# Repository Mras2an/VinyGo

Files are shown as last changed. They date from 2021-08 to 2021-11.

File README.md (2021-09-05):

# VinyGo

## What is VinyGo
VinyGo is an open hardawe, meca, and source project to make a vinyl recorder. Please read the documentations in "doc" repertory.

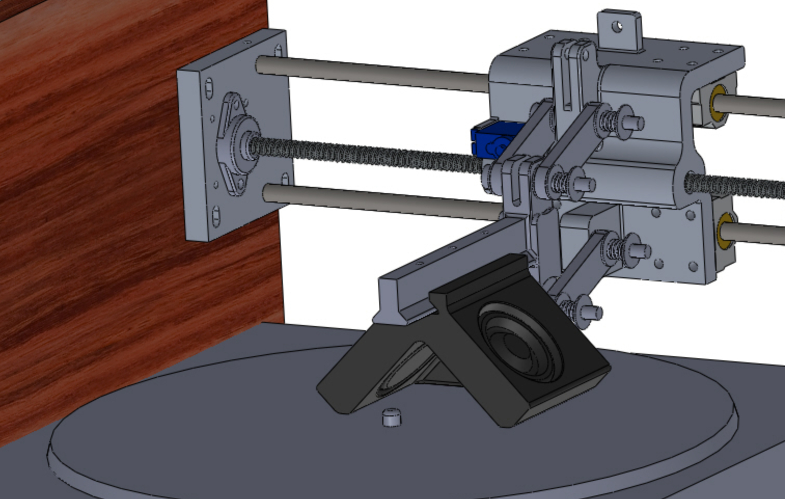
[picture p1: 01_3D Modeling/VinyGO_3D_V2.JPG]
VinyGo


## Project architecture
```
.
├── 00_Doc
├── 01_3D Modeling
├── 02_Hardware
├── 03_Software
└── 04_Utils
```

Doc: All the documentations is in there.

3D Modeling: all 3D files.

Hardware: All hardware files.

Software: This is the full code for the WROOM32 MCU module and LCD.

Utils: it is a set of essential tools for the project.

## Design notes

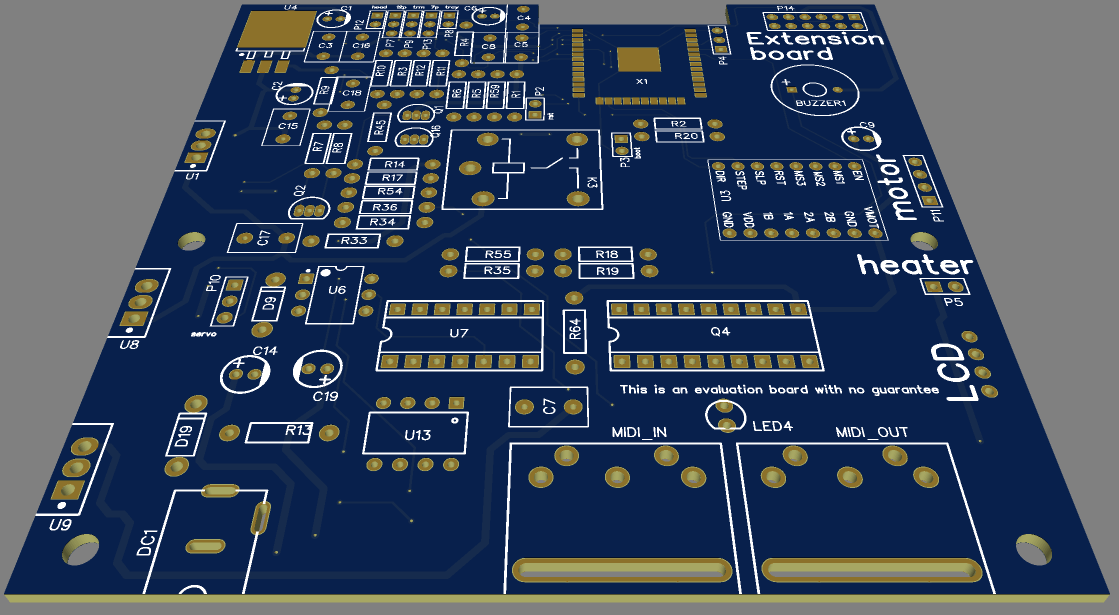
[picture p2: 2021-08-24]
02_Hardware/VinyGo_PCB.png

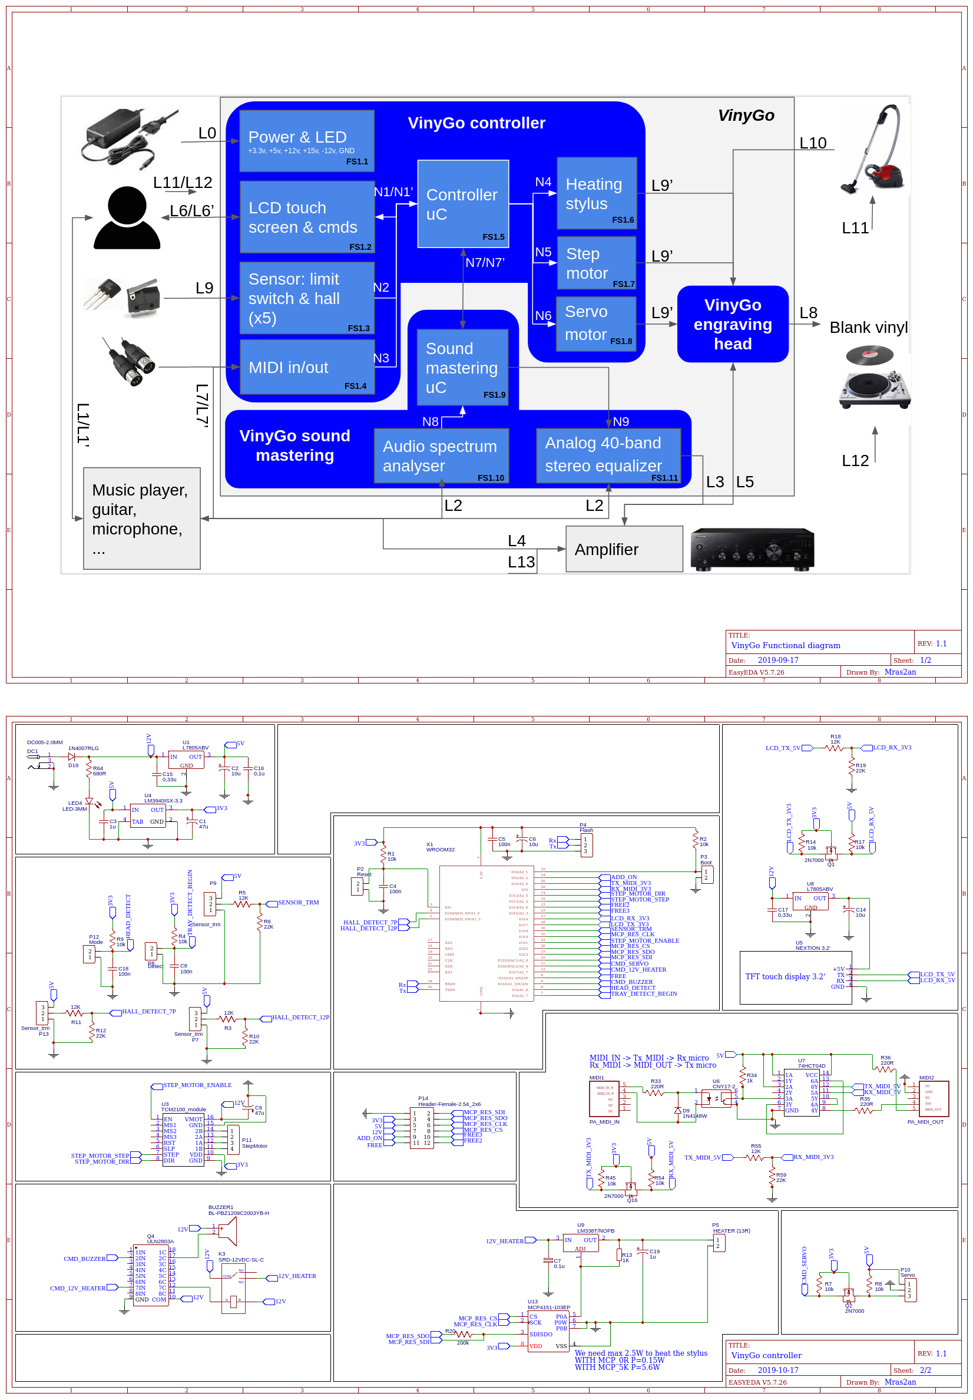
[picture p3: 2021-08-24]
02_Hardware/VinyGo_Schematic.png

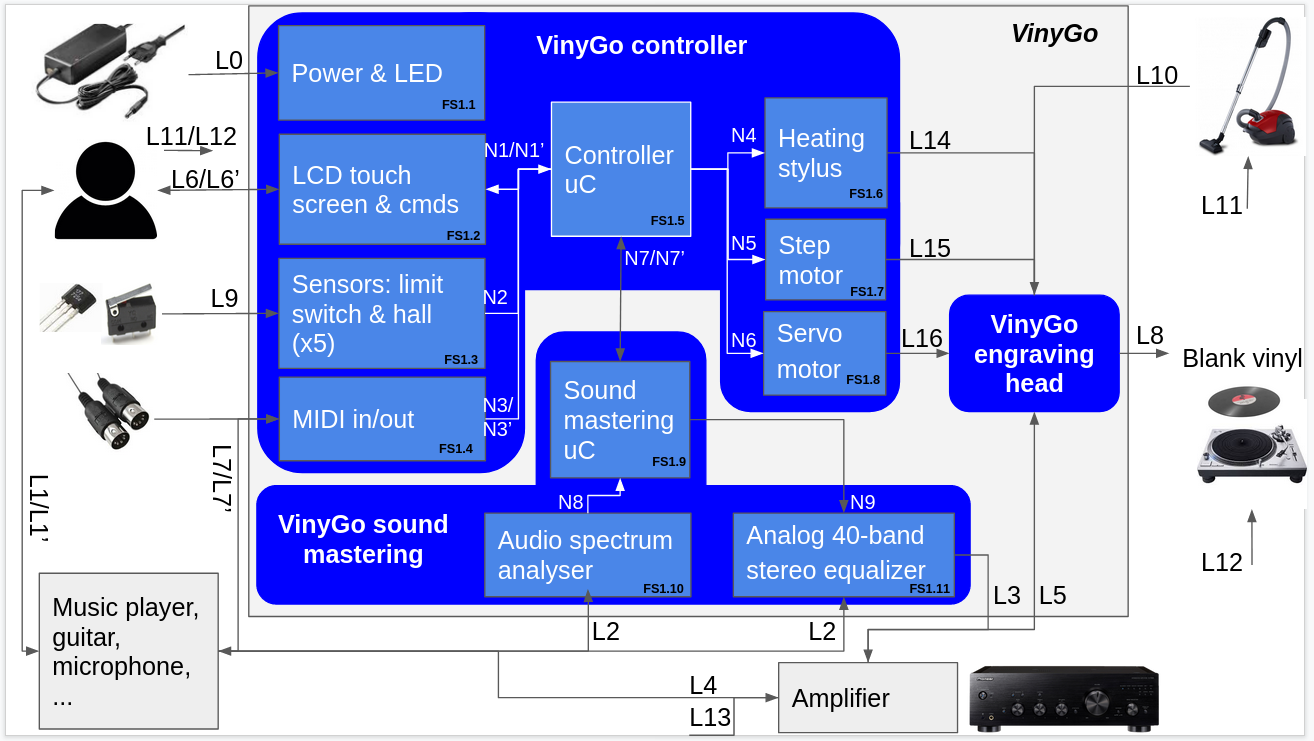
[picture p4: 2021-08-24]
00_Doc/Img/VinyGo_SF.png

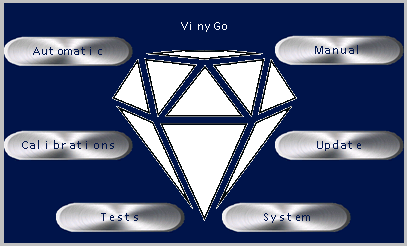
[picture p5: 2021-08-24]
03_Software/LCD_Nextion/vinyGoMenu.png

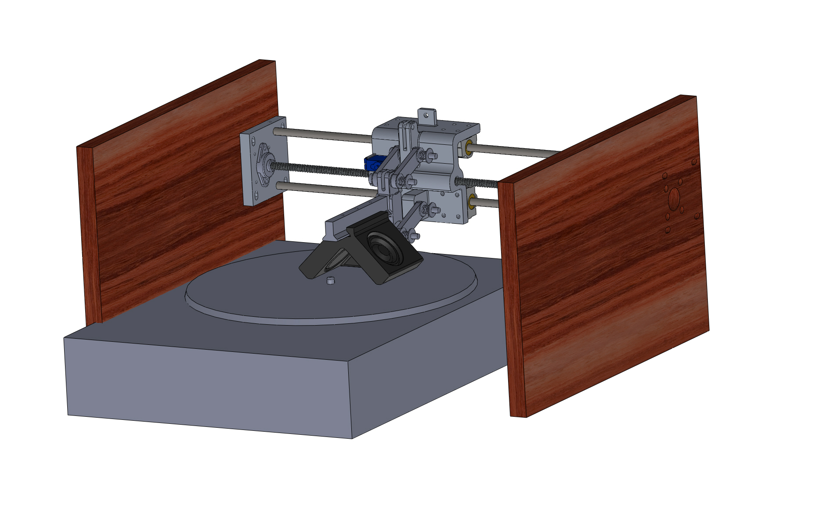
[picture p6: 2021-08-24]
01_3D Modeling/VinyGO_3D.JPG

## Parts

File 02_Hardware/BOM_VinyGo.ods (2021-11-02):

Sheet: Feuille1
ID | Name | Designator | Footprint | Quantity | Manufacturer Part | Manufacturer | Supplier | Supplier Part | Price Uni | Price
1 | WROOM32 | X1 | WROOM32 | 1 | ? |  |  |  | 4,4 | 4,4
2 | L7805ABV | U1,U8 | TO-220(TO-220-3) | 2 | L7805ABV | STMicroelectronics | LCSC | C16807 | 0,9 | 1,8
3 | TCM2100_module | U3 | A4988 STEPPER MOTOR DRIVER CARRIER | 1 | ? |  |  |  | 8 | 8
4 | LM3940ISX-3.3 | U4 | TO-263-3 | 1 | LM3940ISX-3.3 | TI | LCSC | C18910 | 0,55 | 0,55
5 | 47u | C1,C9 | CAP-D5.0XF2.0 | 2 | ? |  |  |  | 0,2 | 0,4
6 | 10u | C2,C6,C14 | CAP-D5.0XF2.0 | 3 | ? |  |  |  | 0,2 | 0,6
7 | 1u | C3 | RAD-0.2 | 1 | ? |  |  |  | 0,2 | 0,2
8 | 10k | R1,R2,R4,R7,R8,R45,R54,R9,R14,R17 | AXIAL-0.4 | 10 | ? |  |  |  | 0,2 | 2
9 | 100n | C4,C5,C8,C18 | RAD-0.2 | 4 | ? |  |  |  | 0,2 | 0,8
10 | Reset | P2 | HDR-1X2/2.54 | 1 | 2.54-1*2PFemale | BOOMELE | LCSC | C49661 | 0,2 | 0,2
11 | Boot | P3 | HDR-1X2/2.54 | 1 | 2.54-1*2PFemale | BOOMELE | LCSC | C49661 | 0,2 | 0,2
12 | Flash | P4 | HDR-3X1/2.54 | 1 | Header2.54mm 1*3P | BOOMELE | LCSC | C49257 | 0,2 | 0,2
13 | Detect | P8 | HDR-1X2/2.54 | 1 | 2.54-1*2PFemale | BOOMELE | LCSC | C49661 | 0,75 | 0,75
14 | Sensor_trm | P13 | HDR-3X1/2.54 | 3 | Header2.54mm 1*3P | BOOMELE | LCSC | C49257 | 0,2 | 0,6
14bis | Sensor_trm | P9,P7,P13 | HDR-3X1/2.54 | 3 | Header2.54mm 1*3P | BOOMELE | LCSC | C49257 | 1,8 | 5,4
15 | 12K | R5,R55,R3,R11,R18 | AXIAL-0.4 | 5 | ? |  |  |  | 0,2 | 1
16 | 22K | R6,R59,R10,R12,R19 | AXIAL-0.4 | 5 | ? |  |  |  | 0,2 | 1
17 | 2N7000 | Q2,Q16,Q1 | TO-92(TO-92-3) | 3 | 2N7000 | CJ | LCSC | C9114 | 0,2 | 0,6
18 | Servo (For V1: srm-120 sanwa, V2 :SG90) | P10 | HDR-3X1/2.54 | 1 | Header2.54mm 1*3P | BOOMELE | LCSC | C49257 | 10 | 10
19 | StepMotor (1.5 A 2.4V 1.8 ° 420mN.m) | P11 | HDR-4X1/2.54 | 1 | Header-Female-2.54_1x4 | ReliaPro | LCSC | C124413 | 7,4 | 7,4
20 | 0,33u | C15,C17 | RAD-0.2 | 2 | ? |  |  |  | 0,2 | 0,4
21 | 0,1u | C16 | RAD-0.2 | 1 | ? |  |  |  | 0,2 | 0,2
22 | CNY17-2 | U6 | DIP-6 | 1 | CNY17-2 | LITEON | LCSC | C10807 | 1,67 | 1,67
23 | 74HCT04D | U7 | DIP-14 | 1 | 74HCT04D | PHILIPS | LCSC | C5958 | 1 | 1
24 | PA_MIDI_IN | MIDI1 | PA_DIN_5_FEMALE | 1 | ? |  |  |  | 2,98 | 2,98
25 | PA_MIDI_OUT | MIDI2 | PA_DIN_5_FEMALE | 1 | ? |  |  |  | 2,98 | 2,98
26 | 220R | R33,R35,R36 | AXIAL-0.4 | 3 | ? |  |  |  | 0,2 | 0,6
27 | 1N4148W | D9 | DO-41 | 1 | 1N4148W | SEMTECH | LCSC | C81598 | 0,25 | 0,25
28 | 1k | R34 | AXIAL-0.4 | 1 | ? |  |  |  | 0,2 | 0,2
29 | 680R | R64 | AXIAL-0.4 | 1 | ? |  |  |  | 0,2 | 0,2
30 | LED-3MM | LED4 | LED-3MM/2.54 | 1 | 204-10SURD/S530-A3 | EVERLIGHT | LCSC | C99772 | 0,2 | 0,2
31 | Alim 12v 2A |  |  | 1 |  |  |  |  | 8,2 | 8,2
31bis | DC005-2.0MM | DC1 | DC-5020 | 1 | DC005-2.0MM | SOFNG | LCSC | C111567 | 0,58 | 0,58
32 | 1N4007RLG | D19 | DO-41 | 1 | 1N4007RLG | ON | LCSC | C53568 | 0,2 | 0,2
33 | NEXTION 3.2' | U5 | NEXTION 3.2' | 1 | NEXTION 3.2' |  |  |  | 32 | 32
34 | Mode | P12 | HDR-1X2/2.54 | 1 | 2.54-1*2PFemale | BOOMELE | LCSC | C49661 | 0,75 | 0,75
35 | LM338T/NOPB | U9 | TO-220(TO-220-3) | 1 | LM338T/NOPB | TI | LCSC | C53303 | 2 | 2
36 | 1K | R13 | AXIAL-0.4 | 1 | ? |  |  |  | 0,2 | 0,2
37 | 0.1u | C7 | RAD-0.2 | 1 | ? |  |  |  | 0,2 | 0,2
38 | MCP4151-103EP | U13 | DIP8 | 1 | ? |  |  |  | 1 | 1
39 | 1u | C19 | CAP-D5.0XF2.0 | 1 | ? |  |  |  | 0,2 | 0,2
40 | HEATER (13R) | P5 | HDR-1X2/2.54 | 1 | 2.54-1*2PFemale | BOOMELE | LCSC | C49661 | 0,2 | 0,2
41 | Header-Female-2.54_2x2 | H2 | DIP-2X2.54MM-4P | 1 | DS1023-2*2SF11 | CONNFLY | LCSC | C92273 | 0 | 0
42 | ULN2803A | Q4 | DIP-18 | 1 | ULN2803A | STMicroelectronics | LCSC | C73936 | 2 | 2
43 | Deco pull up | P1,P6 | HDR-1X2/2.54 | 2 | 2.54-1*2PFemale | BOOMELE | LCSC | C49661 | 0,2 | 0,4
44 | GND_LCD | P17 | HDR-1X1/2.54 | 1 | Header-Male-2.54_1x1 | ReliaPro | LCSC | C81276 | 0 | 0
45 | 200k | R20 | AXIAL-0.4 | 1 | ? |  |  |  | 0,2 | 0,2
46 | SRD-12VDC-SL-C | K3 | SONGLE RELAY SRD FOOTPRINT | 1 | Songle |  |  | undefined | 2 | 2
47 | BL-PBZ1209C2003YB-H | BUZZER1 | BUZZER-R6.0-2P-6.5PITCH | 1 | BL-PBZ1209C2003YB-H | Dongguan Bolin Elec | LCSC | C187885 | 0,35 | 0,35
48 | Header-Female-2.54_2x6 | P14 | HDR-6X2/2.54 | 1 | Header-Female-2.54_2x6 | BOOMELE | LCSC | C36191 | 0,2 | 0,2
49 | PCB |  |  | 1 |  |  |  |  | 2 | 2
50 | radiateur |  |  | 3 |  |  |  |  | 0,215 | 0,645
51 | cable midi |  |  | 2 |  |  |  |  | 2,92 | 5,84
 | nappe cable |  |  | 15 |  |  |  |  | 0,095 | 1,425
total |  |  |  |  |  |  |  |  |  | 117,37

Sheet: Feuille2
Name | Quantity | Price
biellette tete v2 percage 64.STL | 4
support tete gravure v2 percage 64.STL | 1
bloc graveur coulissant v2 percage 64.STL | 1
tete haut parleur v2.STL | 1
platine 3 axes coté moteur(1).STL | 2
 |  | 972,29 PAGF | 870,59 PA

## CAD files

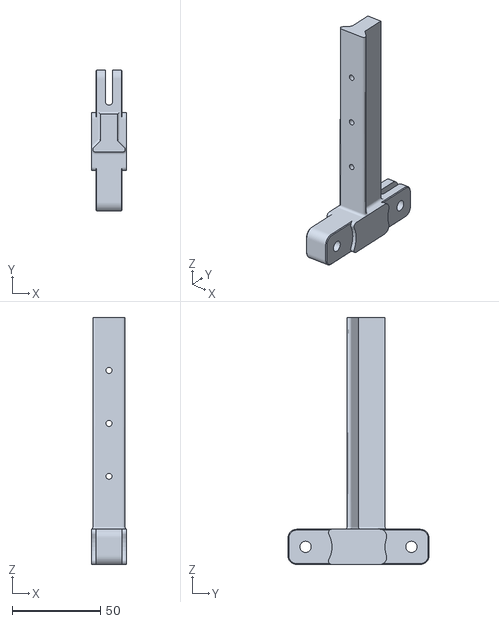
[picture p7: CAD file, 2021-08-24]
01_3D Modeling/STL/V2/support tete gravure v2 percage 6.4.STL
20.0 x 80.0 x 140.0

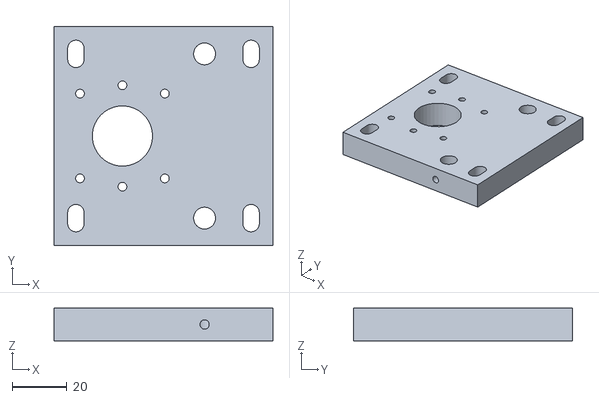
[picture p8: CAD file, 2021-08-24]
01_3D Modeling/STL/V2/platine 3 axes coté moteur(1).STL
80.0 x 80.0 x 12.0

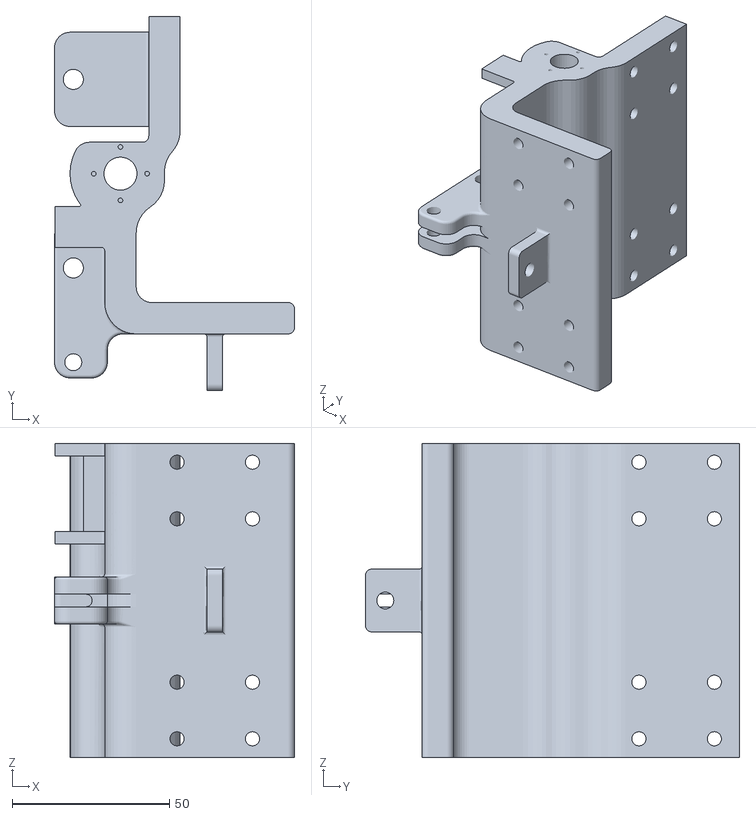
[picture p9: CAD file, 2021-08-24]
01_3D Modeling/STL/V2/bloc graveur coulissant v2 percage 6.4.STL
76.4 x 119.0 x 100.0

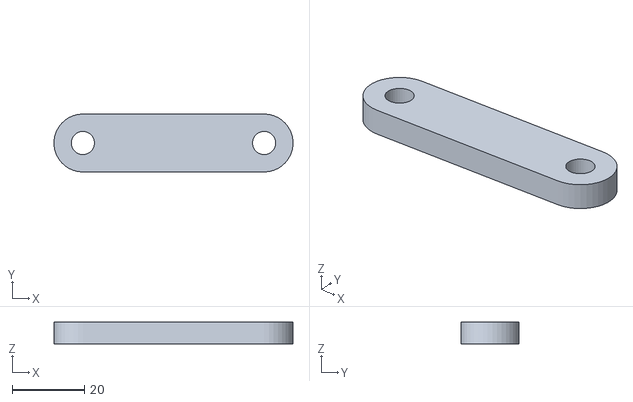
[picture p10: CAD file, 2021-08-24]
01_3D Modeling/STL/V2/biellette tete v2 percage 6.4.STL
65.9 x 16.0 x 6.00

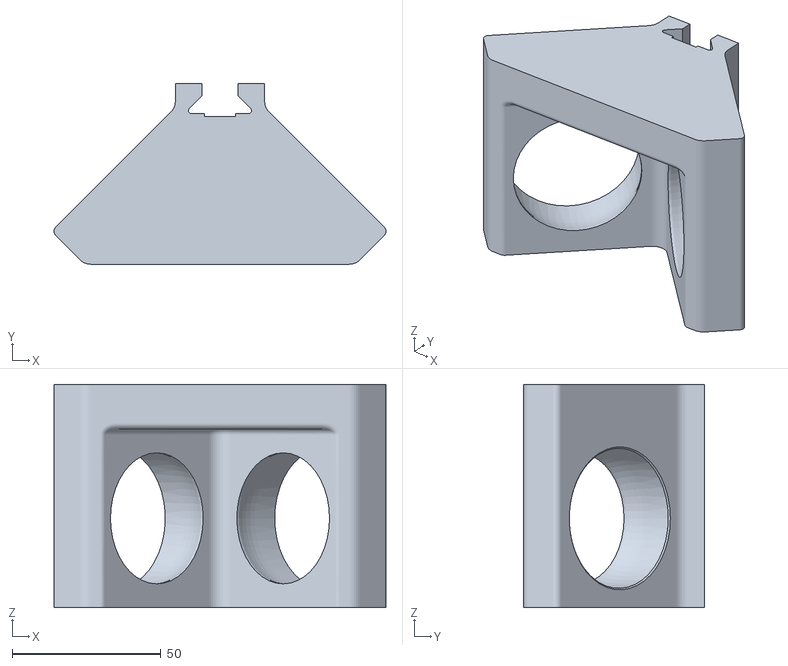
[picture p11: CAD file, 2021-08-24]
01_3D Modeling/STL/V2/tete haut parleur v2.STL
111.5 x 60.6 x 75.0

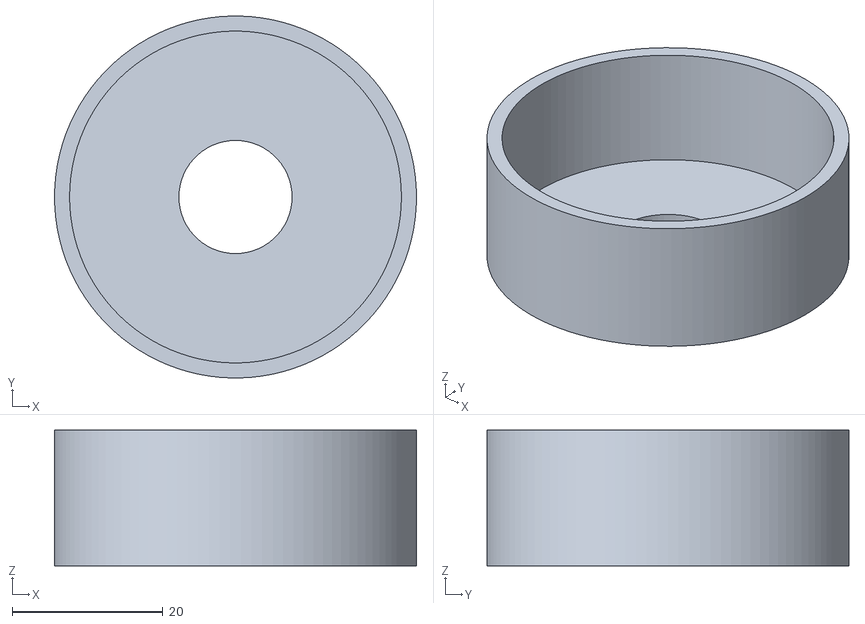
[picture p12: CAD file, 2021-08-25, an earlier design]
01_3D Modeling/STL/V1/contrepoid.stl
48.0 x 48.0 x 18.0

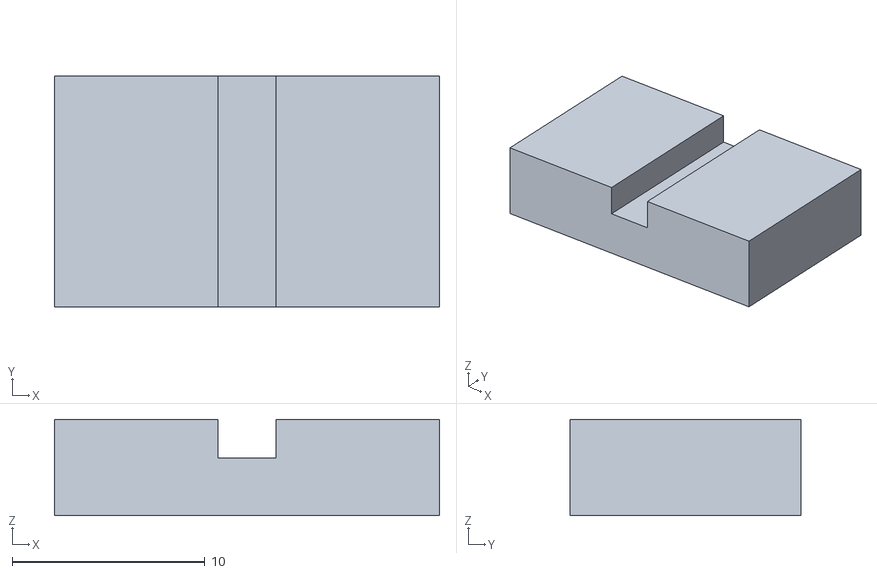
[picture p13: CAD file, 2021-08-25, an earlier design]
01_3D Modeling/STL/V1/contrepoidPush.stl
20.0 x 12.0 x 5.00

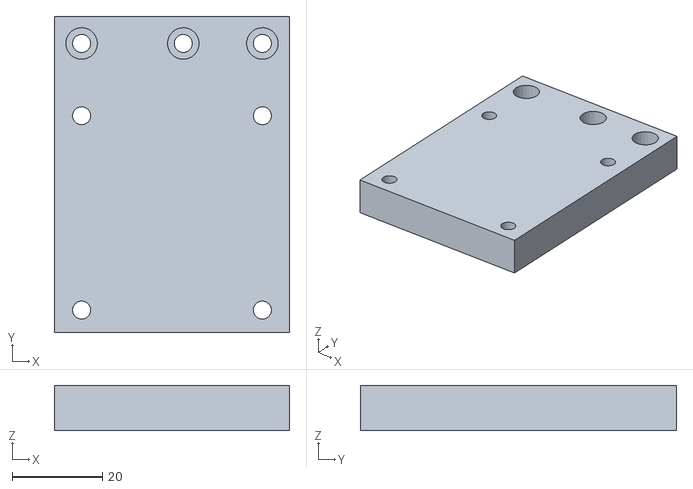
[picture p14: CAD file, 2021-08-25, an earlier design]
01_3D Modeling/STL/V1/trayToHead.stl
52.0 x 70.0 x 10.0

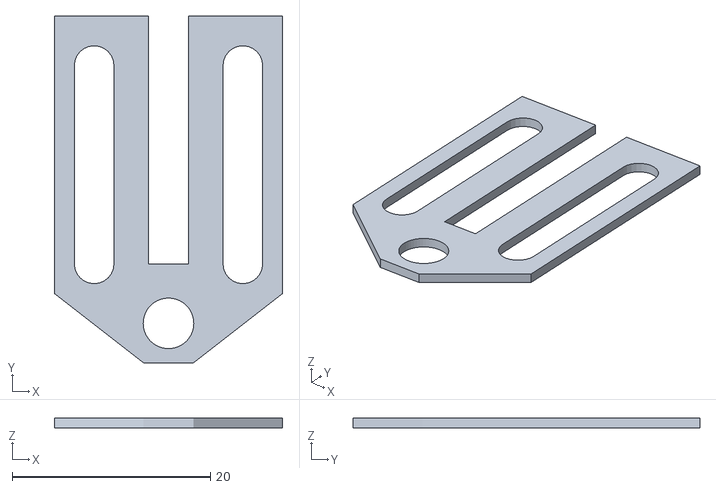
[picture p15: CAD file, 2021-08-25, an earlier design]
01_3D Modeling/STL/V1/fixPointe.stl
23.0 x 35.0 x 1.00

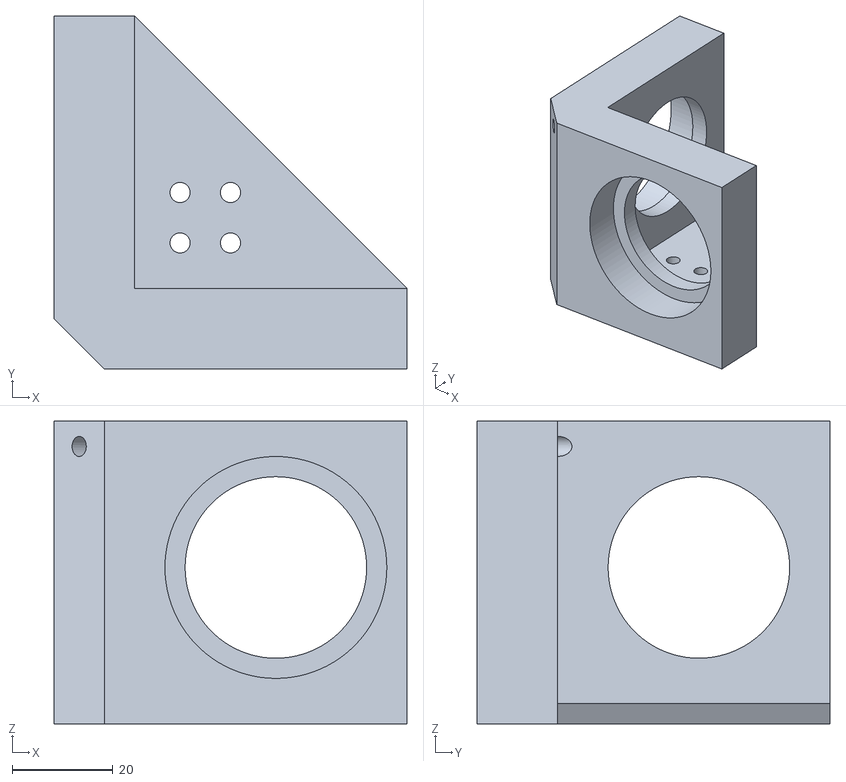
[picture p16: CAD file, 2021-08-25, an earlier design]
01_3D Modeling/STL/V1/teteSound.stl
70.0 x 70.0 x 60.0

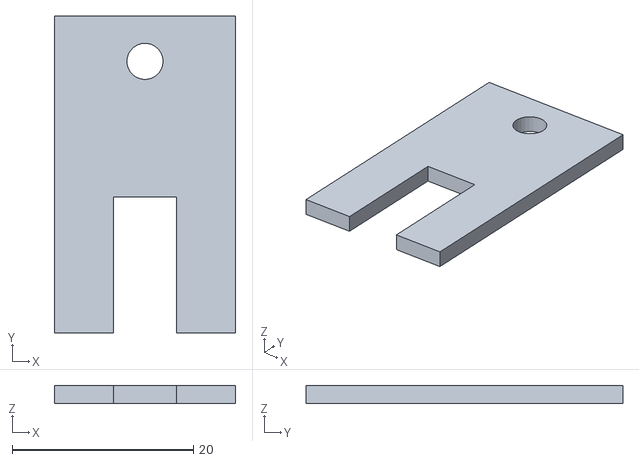
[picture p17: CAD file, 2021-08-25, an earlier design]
01_3D Modeling/STL/V1/detect7or12p.stl
20.0 x 35.0 x 2.00

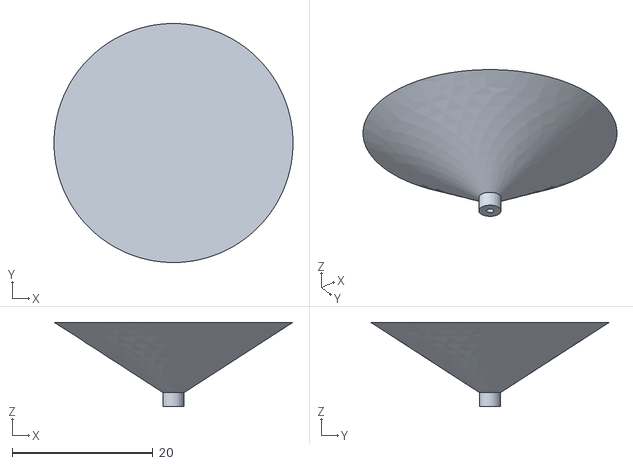
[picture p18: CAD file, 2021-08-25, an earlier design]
01_3D Modeling/STL/V1/cone.stl
34.0 x 34.0 x 12.0

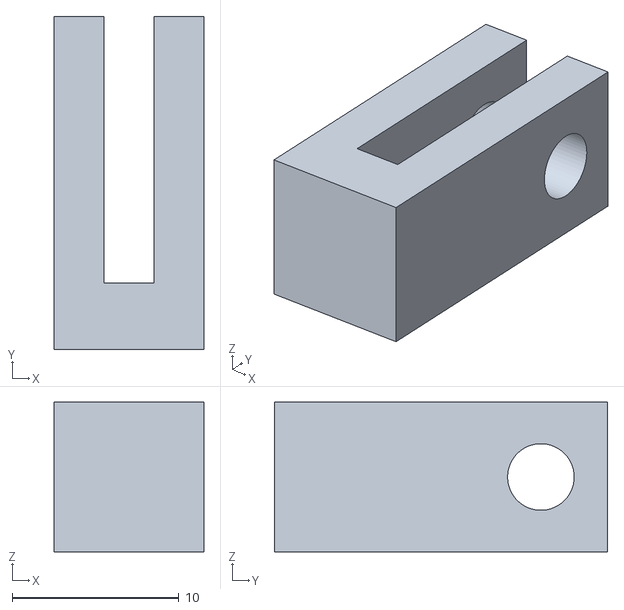
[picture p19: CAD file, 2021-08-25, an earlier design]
01_3D Modeling/STL/V1/fixAxeServo.stl
9.00 x 20.0 x 9.00

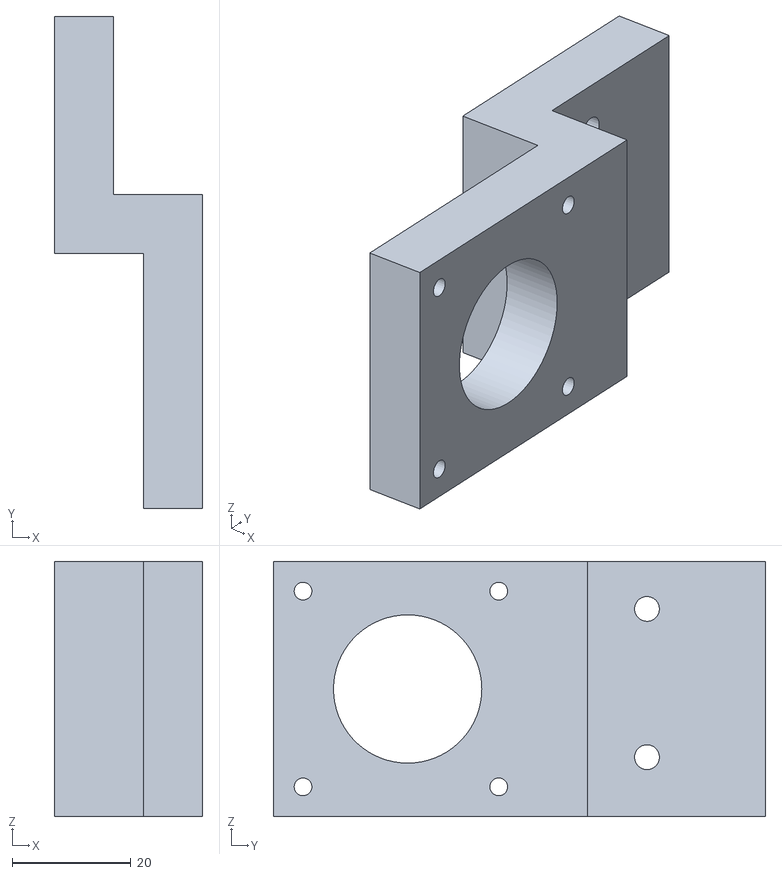
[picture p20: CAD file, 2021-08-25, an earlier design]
01_3D Modeling/STL/V1/fixStepMotor.stl
25.0 x 83.0 x 43.0

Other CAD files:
01_3D Modeling/STL/V1/plateauV3.stl
01_3D Modeling/STL/V1/struct_axeX.stl
01_3D Modeling/STL/V1/finDeCource.stl
01_3D Modeling/STL/V1/fixBull.stl
01_3D Modeling/STL/V1/conneSpeaker2.stl
01_3D Modeling/STL/V1/detectEnd.stl
01_3D Modeling/STL/V1/fixRessort.stl
01_3D Modeling/STL/V1/fixTete.stl
01_3D Modeling/STL/V1/teteSoundV2.stl

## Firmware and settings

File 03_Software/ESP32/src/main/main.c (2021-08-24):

#include "Wifi.h"
#include "System.h"
#include "Initialize.h"
#include "CpuDelay.h"
#include "Gpio.h"
#include "MotorHandling.h"

/******************************************************************************
 * \fn      void app_main(void)
 * \param   void
 * \return  void
 *******************************************************************************/
void app_main(void)
{
    Initialize_init();
    Debug_info("Free Heap at %d = %d\n", __LINE__, OsGetFreeHeapSize());
    System_init();
    Debug_info("Free Heap at %d = %d\n", __LINE__, OsGetFreeHeapSize());
}

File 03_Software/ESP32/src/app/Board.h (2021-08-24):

#ifndef _BOARD_H_
#define _BOARD_H_

#include "Gpio.h"

#ifdef ESP32
    /*  INPUT: Addon*/
    #define ADD_ON                 VR_GPIO_NUM_2

    /*  OUTPUT/INPUT: for MIDI */
    #define TX_MIDI_3V3            VR_GPIO_NUM_4
    #define RX_MIDI_3V3            VR_GPIO_NUM_5

    /*  OUTPUT/INPUT: for LCD */
    #define TX_LCD_3V3             VR_GPIO_NUM_17
    #define RX_LCD_3V3             VR_GPIO_NUM_16

    /*  OUTPUT/INPUT: for Heater */
    #define CMD_HEATING_12V        VR_GPIO_NUM_27
    #define MCP_RES_CLK            VR_GPIO_NUM_19
    #define MCP_RES_CS             VR_GPIO_NUM_22
    #define MCP_RES_SDO            VR_GPIO_NUM_23
    #define MCP_RES_SDI            VR_GPIO_NUM_25
    #define PIN_NUM_MISO MCP_RES_SDO //SDO
    #define PIN_NUM_MOSI MCP_RES_SDI //SDI
    #define PIN_NUM_CLK  MCP_RES_CLK //clk

    /*  OUTPUT/INPUT: for VACUUM */
    #define VACUUM_CMD_BP1         VR_GPIO_NUM_32
    #define VACUUM_CMD_BP2         VR_GPIO_NUM_33

    /*  OUTPUT: cmd for CC motor*/
    #define CMD_MOTOR_EN1          VR_GPIO_NUM_15
    #define CMD_MOTOR_INA1         VR_GPIO_NUM_14

    /* INPUT: sensor, and switch */
    #define SENSOR_TRM             VR_GPIO_NUM_18
    #define HEAD_DETECT            VR_GPIO_NUM_34
    #define HALL_DETECT_7P         VR_GPIO_NUM_36
    #define HALL_DETECT_12P        VR_GPIO_NUM_39
    #define TRAY_DETECTION         VR_GPIO_NUM_35

    /* OUTPUT: cmd for step motor */
    #define STEP_MOTOR_DIR         VR_GPIO_NUM_12
    #define STEP_MOTOR_STEP        VR_GPIO_NUM_13
    #define STEP_MOTOR_ENABLE      VR_GPIO_NUM_21

    /* OUTPUT: Servo motor cmd */
    #define CMD_SERVO              VR_GPIO_NUM_26
#else
    #error "board/hardware is not defined"
#endif


#endif /* _BOARD_H_ */

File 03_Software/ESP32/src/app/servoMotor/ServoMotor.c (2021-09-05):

#include "ServoMotor.h"
#include "FileSystem.h"
#include "Board.h"
#include "System.h"
#include "MotorHandling.h"
#include "CpuDelay.h"
#include "Debug.h"
#include "ModeCalibration.h"


typedef struct ServoMotor_t {
    int direction;
} ServoMotor;

ServoMotor ServoMotor_t;
#define this (&ServoMotor_t)


void ServoMotor_init()
{
    if(ServoMotor_getDirection()) {
        this->direction = 1;
        Debug_info("Servo motor inverted\n");
    } else {
        this->direction = 0;
        Debug_info("Servo motor not inverted\n");
    }
}

void ServoMotor_toggleDirection()
{
    char * servo = Fs_read(FILE_NAME_SERVO_MOTOR, FILE_NAME_SERVO_MOTOR);

    if(servo != NULL)  {
        OsFree(servo);
        this->direction = 0;
        Debug_info("Servo motor not inverted\n");
        Fs_delete_all(FILE_NAME_SERVO_MOTOR);
    } else {
        this->direction = 1;
        Debug_info("Servo motor inverted\n");
        Fs_write(FILE_NAME_SERVO_MOTOR, "true", FILE_NAME_SERVO_MOTOR);
    }
}

int ServoMotor_getDirection()
{
    char * servo = Fs_read(FILE_NAME_SERVO_MOTOR, FILE_NAME_SERVO_MOTOR);

    if(servo != NULL)  {
        OsFree(servo);
        return 1;
    }

    return 0;
}

void ServoMotor_getUpOrDown(char * buffer)
{
    uint32_t sensor[2] = {0x00, 0x00};
    Gpio_get(HEAD_DETECT, &sensor[0]);

    //up
    if(sensor[0])
        memcpy(buffer, "Down", 4);
    else
        memcpy(buffer, "Up", 2);
}

void ServoMotor_up()
{
    Debug_info("Servo motor up\n");

    if(this->direction == 0) {
        MotorHandling_startServo(50, ModeCalibration_getValForServoUp());
    } else {
        Debug_err("NEED TO BE CODED");
    }

    CpuDelay_ms(200);
}

void ServoMotor_down()
{
    Debug_info("Servo motor down\n");

    if(this->direction == 0) {
        for(float i = 5; i <= ModeCalibration_getValForServoDown(); i = i + 0.1) {
            MotorHandling_startServo(50, i);
            CpuDelay_ms(75);
        }
    } else {
        Debug_err("NEED TO BE CODED");
    }
}

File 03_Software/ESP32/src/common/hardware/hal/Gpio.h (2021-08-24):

#ifndef _GPIO_H_
#define _GPIO_H_

#include "Bsp.h"

typedef enum eGpioNum {
    VR_GPIO_NUM_0=0,
    VR_GPIO_NUM_1,
    VR_GPIO_NUM_2,
    VR_GPIO_NUM_3,
    VR_GPIO_NUM_4,
    VR_GPIO_NUM_5,
    VR_GPIO_NUM_6,
    VR_GPIO_NUM_7,
    VR_GPIO_NUM_8,
    VR_GPIO_NUM_9,
    VR_GPIO_NUM_10,
    VR_GPIO_NUM_11,
    VR_GPIO_NUM_12,
    VR_GPIO_NUM_13,
    VR_GPIO_NUM_14,
    VR_GPIO_NUM_15,
    VR_GPIO_NUM_16,
    VR_GPIO_NUM_17,
    VR_GPIO_NUM_18,
    VR_GPIO_NUM_19,
    VR_GPIO_NUM_20,
    VR_GPIO_NUM_21,
    VR_GPIO_NUM_22,
    VR_GPIO_NUM_23,
    VR_GPIO_NUM_24,
    VR_GPIO_NUM_25,
    VR_GPIO_NUM_26,
    VR_GPIO_NUM_27,
    VR_GPIO_NUM_28,
    VR_GPIO_NUM_29,
    VR_GPIO_NUM_30,
    VR_GPIO_NUM_31,
    VR_GPIO_NUM_32,
    VR_GPIO_NUM_33,
    VR_GPIO_NUM_34,
    VR_GPIO_NUM_35,
    VR_GPIO_NUM_36,
    VR_GPIO_NUM_37,
    VR_GPIO_NUM_38,
    VR_GPIO_NUM_39,
    VR_GPIO_NUM_MAX = 40,
} eGpioNum_t;


typedef enum eGpioMode {
    VR_GPIO_MODE_INPUT,
    VR_GPIO_MODE_OUTPUT,
    VR_GPIO_MODE_OUTPUT_OPEN_DRAIN,
    VR_GPIO_MODE_INPUT_OUTPUT,
    VR_GPIO_MODE_INPUT_OUTPUT_OPEN_DRAIN,
} eGpioMode_t;

typedef enum eGpioPull {
    VR_GPIO_PULL_NONE,
    VR_GPIO_PULL_UP,
    VR_GPIO_PULL_DOWN,
} eGpioPull_t;

typedef enum eGpioLevel {
    VR_LEVEL_LOW,
    VR_LEVEL_HIGH,
} eGpioLevel_t;


#ifdef ESP32
    #include "Esp32Gpio.h"
    #define Gpio_init       Esp32Gpio_init
    #define Gpio_destroy    Esp32Gpio_destroy
    #define Gpio_configure  Esp32Gpio_configure
    #define Gpio_set        Esp32Gpio_set
    #define Gpio_get        Esp32Gpio_get
    #define Gpio_toggle     Esp32Gpio_toggle
#else
    #error "board/hardware is not defined"
#endif

#endif // _GPIO_H_

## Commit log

2021-08-24 project: initial commit.
    [biellette tete v2 percage 6.4.STL, bloc graveur coulissant v2 percage 6.4.STL, customPart.csv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]
2021-08-25 add V1 stl files.
    [cone.stl, conneSpeaker2.stl, contrepoid.stl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]
2021-10-27 add bom.
    [BOM_VinyGo.ods]
2021-11-02 add ref for motor and servo.
    [BOM_VinyGo.ods]
